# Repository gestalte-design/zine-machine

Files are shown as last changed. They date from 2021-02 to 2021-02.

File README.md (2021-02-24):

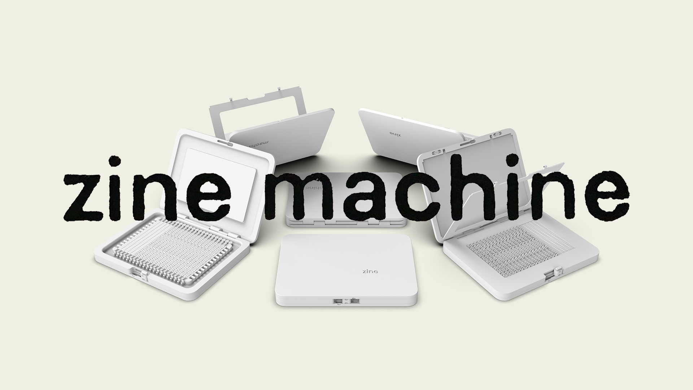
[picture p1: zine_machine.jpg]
image of the zine machine

# zine machine is a compact 3d-printed block printing press. 

Convert images into blocks, try friends' blocks, or use the supplied type to set a page.

All files and instructions necessary to print and use a zine machine are open to the public and available on this website.

Zine Machine is an experiment in guerilla digital fabrication by [Gestalte Design](https://gestalte.design)

# Table of Contents

- [Step-by-Step Instructions](#step-by-step)
  - [Supplies Not Included](##supplies-not-included)
- [FAQ](#FAQ)
  - [Printing the Zine Machine](##printing-the-zine-machine)
  - [Creating Custom Plates](##creating-custom-plates)
- [Contact](#contact) 

# Step-by-Step Instructions

## Supplies Not Included

1. Brayer — a kind of roller you would use for a lino plate.
2. Ink — any kind of ink, the kind you would use for block printing.

## Zine Machine Basic Setup
1. Print out the parts for the zine machine. You'll need access to a 3D printer, of course. Or, if you want you can send the stl files to a 3rd party for printing.
   1. Note that you will need to slice these stl files first before you bring them to a 3d printer. We recommend using [slic3r](https://slic3r.org/). You can find instructions on how to do this on their website.
2. Follow the assembly instructions found [here](Instructions/zine-machine-assembly.pdf).
3. (optional) Clamp the zine machine down for a day or two before use the plastic tends to bend very slightly.

## Zine Machine Custom Image Plates
Many 3D software prorams allow you to drop in a 2d vector and "pull" it into the third dimension. If you can imagine you have a black and white image. All the white pixels are "0mm" height and all the black pixels are "3mm" height. That's effectively how it works.

You can find the instructions [here](Instructions/creating-plates.pdf).

# FAQ

This FAQ will expand as we encounter more questions. Feel free to make a pull request to add some yourself.

## Printing the Zine Machine

#### Q: Can I just buy a zine machine from you?
At the moment, we don't have the ability to provide this service.

#### Q: What 3D printer do you recommend?
We used a Prusa MK3S+ — the settings were calibrated for this printer and will work the best.

## Creating Custom Plates

#### Q: What kind of images can I use?

Look at woodcuts or linocuts for some inspiration. Be careful when trying to print an image with very thin lines or lots of complex intersections. If you hope to push the limits of your design, you'll want to know the thickness of the nozzle on your 3D printer.

#### Q: I don't have adobe illustrator!

You can find many "vectorizers" online. We've used [rapid resizer](https://online.rapidresizer.com/tracer.php) before.

# Contact

You may fill out issues here on the GitHub, of course.

or DM us on [Twitter](https://twitter.com/gestalte_design) or [Instagram](https://instagram.com/gestalte.design)

# License

Software License is MIT

<p xmlns:dct="http://purl.org/dc/terms/" xmlns:vcard="http://www.w3.org/2001/vcard-rdf/3.0#">
  <a rel="license"
     href="http://creativecommons.org/publicdomain/zero/1.0/">
    
  </a>
  <br />
  To the extent possible under law,
  <a rel="dct:publisher"
     href="https://github.com/gestalte-design/zine-machine">
    <span property="dct:title">Gestalte Design</span></a>
  has waived all copyright and related or neighboring rights to
  <span property="dct:title">Zine Machine</span>.
This work is published from:
<span property="vcard:Country" datatype="dct:ISO3166"
      content="US" about="https://github.com/gestalte-design/zine-machine">
  United States</span>.
</p>

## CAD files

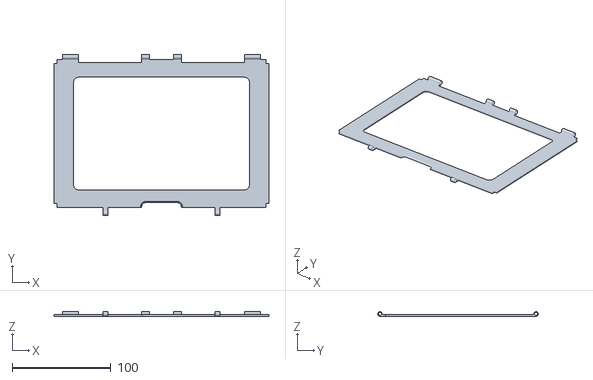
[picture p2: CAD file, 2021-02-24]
ZineMachineParts/Body/paper frame.stl
217.6 x 162.6 x 4.80

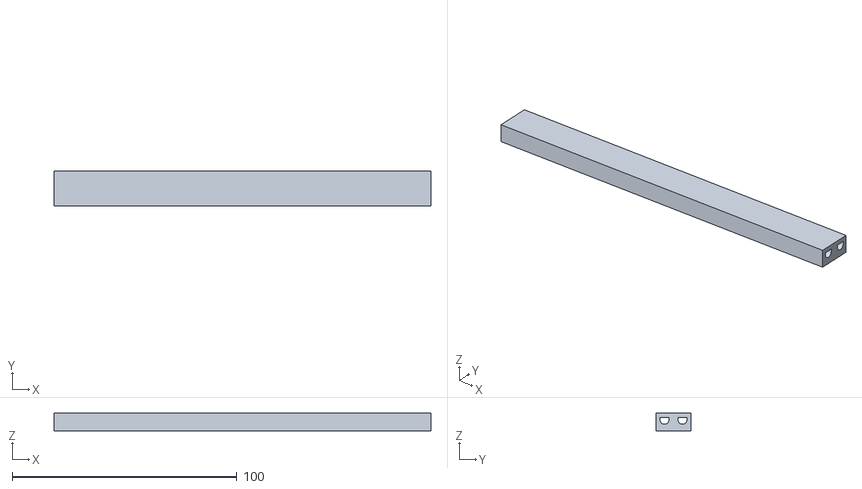
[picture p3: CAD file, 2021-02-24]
ZineMachineParts/LettersPlatesSpacers/plates stl/2 21.stl
167.6 x 15.6 x 8.00

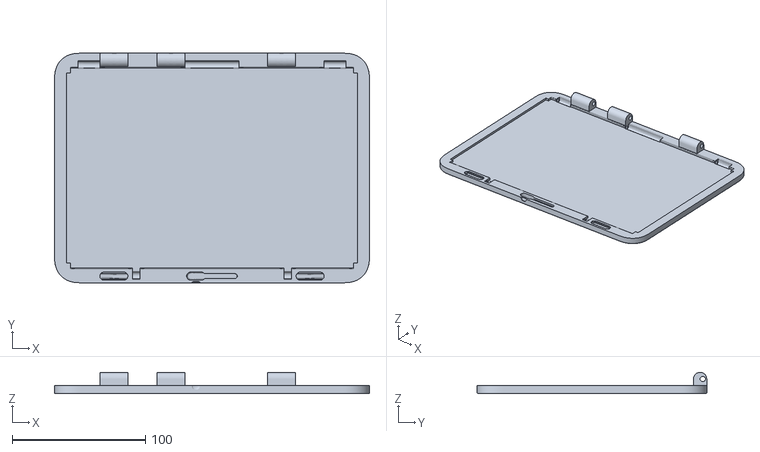
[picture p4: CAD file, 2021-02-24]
ZineMachineParts/Body/machine lid.stl
236.0 x 172.0 x 16.0

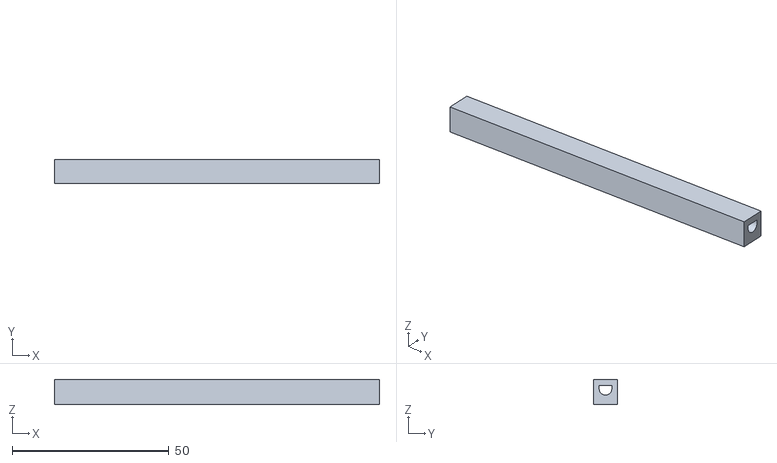
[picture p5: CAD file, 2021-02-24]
ZineMachineParts/LettersPlatesSpacers/plates stl/1 13.stl
103.6 x 7.60 x 8.00

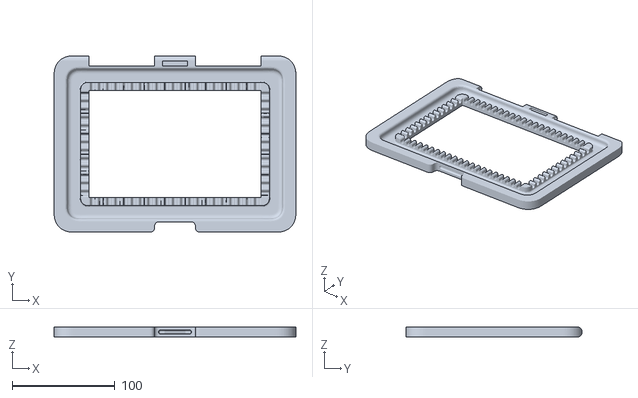
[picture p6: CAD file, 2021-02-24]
ZineMachineParts/Body/body.stl
236.0 x 172.0 x 10.0

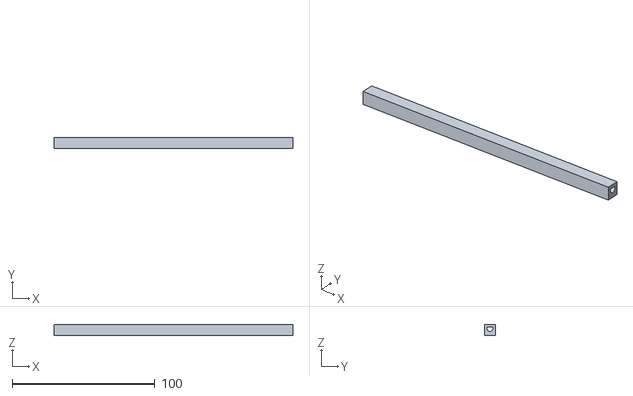
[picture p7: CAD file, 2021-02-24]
ZineMachineParts/LettersPlatesSpacers/plates stl/1 21.stl
167.6 x 7.60 x 8.00

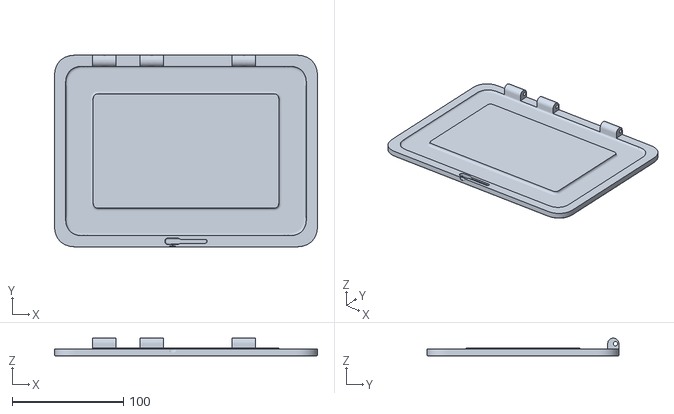
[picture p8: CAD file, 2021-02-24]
ZineMachineParts/Body/zine lid.stl
236.0 x 172.0 x 16.0

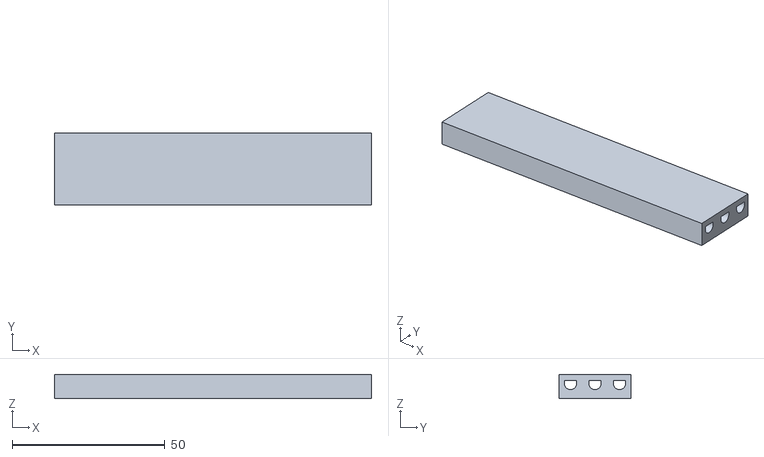
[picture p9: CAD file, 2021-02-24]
ZineMachineParts/LettersPlatesSpacers/plates stl/3 13.stl
103.6 x 23.6 x 8.00

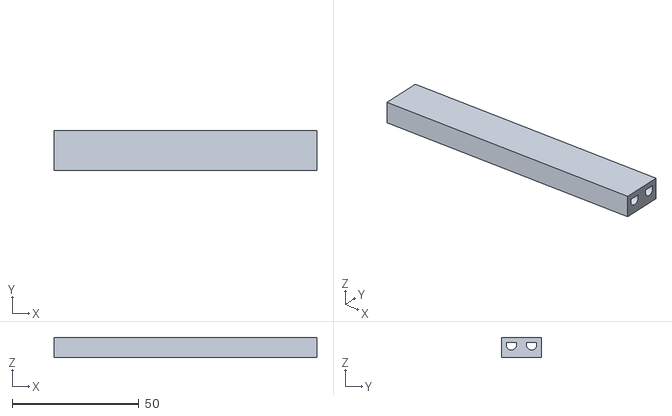
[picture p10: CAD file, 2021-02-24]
ZineMachineParts/LettersPlatesSpacers/plates stl/2 13.stl
103.6 x 15.6 x 8.00

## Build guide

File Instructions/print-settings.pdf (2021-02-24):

0.4mm nozzle, PLA

0.15 layer height
0.2 first layer height
2 perimeters (1 when printing letters) minimum 3 solid layers on top and bottom rear seam position

minimum 15% fill density
combine infill every 1 layer
draft shield only when printing letters and linkage supports when printing lock and paper frame slides, from the build plate only

0.45mm extrusion width
0.4mm extrusion width for top solid infill

infill/perimeters overlap 25%
0.2mm elephant foot compensation

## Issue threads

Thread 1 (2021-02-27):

letter and spacers are massive

khusmann, 2021-02-27:
Hello, thanks for this project! I'm trying to print the letters and spacers stl but it keeps crashing my slicer -- my machine is too pokey to even open the STL cut into pieces to even have a chance at it. any chance you'd be willing to split the massive STL into say, 4 smaller groups of letters w their own stl? (or maybe make one row of letters its own STL, and one row of spacers its own STL and I can keep adding until I run out of memory...)

Thanks!

jasonkgreen, 2021-03-01:
If you don't mind wish list items, a single spacer , either as some editable file format or a schematic with measurements, would facilitate those who wished to add additional type options.

briandavism, 2021-03-01:
Using a .3MF file in addition to the .stl files could keep the file size down and embed the recommended print settings especially for the letter and spacers since each instance of a letter would not increase the file size. Personally I would love split letters so I could print what I actually need.

gavin-owens, 2021-03-01:
I've heard this already from others. This just makes sense. Would one of you be willing to take this on? I wouldn't be able to get to it immediately.

jasonkgreen, 2021-03-03:
>
>
> I've heard this already from others. This just makes sense. Would one of you be willing to take this on? I wouldn't be able to get to it immediately.

I've got a 3MF of the whole letters and spacers file made and a single spacer object in several formats.  Unfortunately I've never opened a pull request, so I'm not sure what to do with them,

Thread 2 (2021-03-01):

Printability: Horizontal Tunnels

briandavism, 2021-03-01:
## Issue
This print has many internal horizontal cylinders which are hard to print, even on well calibrated printers. There are two main reasons for this especially when relying on the horizontal tunnels to act as hinges as they are here.

1. The stair stepping inherent to FDM printing on any curve along the XZ and YZ planes. Ideally if you are printing hinges it works best to place any smooth curves along the XY planes. these stair steps will cause ratcheting and jamming on the hinge.
2. the 90° overhang at the top of the cylinder will always drooping

In the photo attached you can see the stair stepping, drooping, and a bulge along the thin edge as well. This print was made with a 0.8mm nozzle which has an even higher tollerance for overhang than your recommended 0.4 nozzle

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

## Recommendations.
For the hinges, the hinge blocks should be printed separately in a different orientation so the cylinder is vertical.

For the tunnels inside of the letters I recommend an alignment hole with a peak. This is a common solution that does not have more than a 45° overhang

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

gavin-owens, 2021-03-03:
The less moving parts the better, in my opinion, so I'm hesitant to move the hinge blocks into a separate piece. Right? Consider we can get a better print, which may have a nicer overall movement and feel to it, but introduces more complexity in the assembly and potentially some weakness into a part of the machine that will be exercised regularly. I don't have any good alternative suggestions here, unfortunately, but overall I think you can get most of the way there with some finishing on the hinges.

As for the alignment hole with the peak, seems like a great suggestion to me. Do you want to test it out on a few letters and see how it works?

briandavism, 2021-03-05:
Yeah I don't mind going in with a drill bit and cleaning up tunnels but some parts (body.stl) have the tunnels positioned in a way which is inaccessible.

I haven't printed the lettersets yet since it is a 2 day print at the .25mm nozzle. (the 0.4 isn't able to print all the letters)

briandavism, 2021-03-05:
This is how I would redesign the hinge blocks. I respect the decision not to use external hardware like screws since they vary globally but I think glue is ok to call for but may not even be necessary if you can get a good friction fit. I have lots of designs that use friction fit butterfly joints and they work fine. I think the benefits of smoother operation and repairability if one of the hinge pins breaks far outweighs the cost of a few extra parts.
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

It's also the case that you can still print the hinge pins horizontally since as long as the tunnel is printed vertically and smooth you will not get the grinding of layers. And since the hinge assembly can be built and then attached to the body you could have a longer single hinge pin and avoid all the fiddly pin assembly so the part count would go down actually.

gavin-owens, 2021-03-09:
Hm, ok, I think you make some really good points. I generally prefer friction fits, because they are more immediate — plus we're trying to avoid the need to acquire any other material for assembly if possible (why we got rid of these tiny springs used in the assembly).

Will bring this proposal to Constantine and see if he has any recommendations. Will try to get back to you in a couple days. Thanks for your patience!

gavin-owens, 2021-03-09:
Hm, ok, I think you make some really good points. I generally prefer friction fits, because they are more immediate — plus we're trying to avoid the need to acquire any other material for assembly if possible (why we got rid of these tiny springs used in the assembly).

Thanks for your patience!

So, Constantine claims he was able to print without any overhang on the hinges. Have you tried to print with the 0.4 nozzle?

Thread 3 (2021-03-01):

Punctuation and Language Support

briandavism, 2021-03-01:
Personally I'm looking for the the letters
ö ä ü ß ð þ
but I'm sure many other languages could be supported with only a few more characters.

Additionally some punctuation would be nice
especially the interrobang ‽ because it is a great character

gavin-owens, 2021-03-03:
Yes, please! I'm excited to expand the language support. We used Helvetica Monospaced to generate the font blocks. If you don't own a license, then perhaps I can add those letters to the file. Not really sure how to share a license for a project like this legally.

briandavism, 2021-03-05:
I'm thinking maybe Helvetica isn't the most suitable font for this project, especially since it brings up the legal issue of sharing actual character blocks for the purpose of printing. Helvetica is also a tough font to 3d print, looking into it I would need to print the character blocks with a .25mm nozzle to print the thin areas.

I've used Pathway Gothic One as a font for 3D printing since it has a consistent line width and no small inner areas.

gavin-owens, 2021-03-09:
I agree that a licensed file isn't ideal for an open-source project, but we are going to keep the helvetica monospace as a font set — that I'm pretty sure is legal.

Add whatever extra fonts you'd like, in this case the more options the better for everyone — maybe just create a new sub folder to organize all the different fonts?

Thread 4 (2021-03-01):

Printability: XZ and YZ curvature

briandavism, 2021-03-01:
In general there are too many curves on the XZ Axis and YZ Axis.

In this pic you can see curved sides coming off the print bed which is the worst case of this issue. on layer 2 the printer will have a large overhang which always results in a flat side of these objects.

In the case of the rods, they could be printed vertically except for the unnecessary fillets on the sides of them

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

In the "rods with clamps" file you did a great job with the print bed overhang, however I still think the alignment of the letters would be even better if you used chamfers on the top as well, but maybe you tested this and it works fine.
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

gavin-owens, 2021-03-03:
It works fine without the chamfers, we've definitely tested the alignment. I think it's acceptable to have some overhang on one side of the rods, because only one side needs to rest into the guides.

So, these changes seem largely cosmetic, which means this can be backlogged — keep it open for more discussion and give Constantine, who is rather busy right now, a chance to consider those changes as well.

What do you think?

briandavism, 2021-03-05:
The hinges are not cosmetic though, overall the whole print feels very crunchy and I'm having trouble getting things printed and fitting together. especially since these rods go into tunnels that are also printed horizontally. and have overhang on the top, plus the crunchyness of all the layer lines working against each other as it is opening and closing. There are some simple fixes that would allow all the hinges to be printed in the best orientation.

gavin-owens, 2021-03-09:
I see, but it seems we can close this thread and work out those problems in #2 — if I'm wrong about that please open a new issue or make a comment here to re-open (if this is proper the issue already) with a proposed change like you did for the hinges. The image you used in the other issue was perfectly clear and sets a good precedent for how to propose a change.

Closed 2021-03-09.

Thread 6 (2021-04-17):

Printability: size

mbravorus, 2021-04-17:
The body and lid STLs are 236mm on the longest axis. which doesn't fit even on an Ender 3 Pro 235x235mm print bed, and shouldn't fit on the recommended Prusa mk3s+ 210x210mm bed either. Unless printed vertically, which would require a ton of support, affect quality and doesn't seem a logical way to go. Could you elaborate on how this was supposed to be printed?

retiolum, 2021-05-10:
The body at least doesn't fit on my Creality CR6-SE, too. Do you have experience with scaling the whole setup (e.g. to 90 %)?
